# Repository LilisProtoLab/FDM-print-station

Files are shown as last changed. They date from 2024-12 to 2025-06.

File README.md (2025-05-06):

# FDM print station
For a number of FDM 3D printing materials it is of importance to store and use them under low relative humidity conditions. 
For this purpose a station was designed, containing an adapter drawer with two storage compartments, and three 3D printer compartments. For each compartment relative humidity (and temperature) can be monitored and controlled by flushing with dried compressed air. 

DSCF2053

## Main features
This FDM print station contains:
+ A humidity control system
	+ Building-supplied compressed air is fed through a membrane dryer (DM08G-19KA-N) to reduce the moisture level
   	+ Each compartment contains a sensor unit which monitors temperature, humidity and door open status
   		+ Door sensors make sure flushing is only active while the compartments are closed
   	+ Five electronic valves direct the flow of pressured air to each compartment
   	+ Dried air is distributed to five compartments: two drawer compartments, and three printer compartments
   	+ Home Assistant integration controls the humidity setpoints for the drawer compartments (typically 12%) and the printer enclosures (typically 20%)
+ One filament storage drawer with two compartments
	+ A pre-existing drawer is supplemented with a transparant PMMA enclosure for convenient selection of materials with the lids closed	
	+ A screen mounted to the drawer displays the current humidity, temperature and door sensors + flushing status of all compartments
+ Three printer enclosures
	+ vertical sliding doors for minimal obstruction from 5mm PMMA sheets, with 3D printed handles and latches.
	+  The exhaust ventilation is connected to the building exhaust system and controlled via manual, 3D printed gate valves.
	+ The enclosure is made from aluminium extrusions with 3mm PMMA sheet walls

```
.
|--- Build 
|--- Docs
|--- Results
|--- Software
| LICENSE
| README.md

```

The purpose of each subfolder is explained below:
+ Build: Contains all the (binary) design files that are needed for the hardware. Use subfolder for more complex assemblies.
+ Docs: Contains the documentation of the project: background information, sources, warnings, and build instructions. 
+ Results: For measurement or functional devices, it is good to report some results as a benchmark for others who try to replicate the project.
+ Software: For hardware projects that have an operating software or firmware, it is a good versioning practice to separate the software code from build instructions.

## Build instructions
_Guide the reader with the order of browsing your project repository for an optimum building experience_
 
When you want to start a new repository, it is better that you copy this repository to your project repository and start by changing all the description.
All instructions and (sub)headers are suggestions. You can change the style, order, or composition as you see necessary. 

It would be kind if you put a shortcut to your Bill of Materials file.
This template can be copied free of charge. 

## Outcomes

## Team
+ Project initiator: Pieter Kooijman @pkooijman
+ Contributors:
	+ Josh Hauser @catoprovector
 	+ Nico van Hijningen

## Get involved
_Especially for open source projects, it is benefitial to motivate the potential users of the project to contribute back or share their feedback. Make it easy for them._

Comments and suggestions on this folder structure are always welcome. Please create an issue to share your feedback or question, or if you prefer send a pull request. 

Better structured projects can explain a number of options for contributors such as: 
+ (where to start)
+ (issue template)
+ (direct contact)
+ (pull requests)

## License
_After the README, A LICENSE is the most important file in the project documentation. Without a license, there is too much uncertainty to try building anything on top of the original project._

This project is released under CC0 1.0 Universal. 
You can modify an reuse as you like.
The project team appreciates your suggestions or examples for enhancing the repository, but your consistent documentation of your project is the best gift to the world. Hopefully, this template could make that a bit easier for you. 

### (How to cite:)
_Additionally, you can specify how other can cite your project._

## (Funding)
_Be kind to your funders and mention their support visibly and consistently. They also need to show their resources are wisely spent._

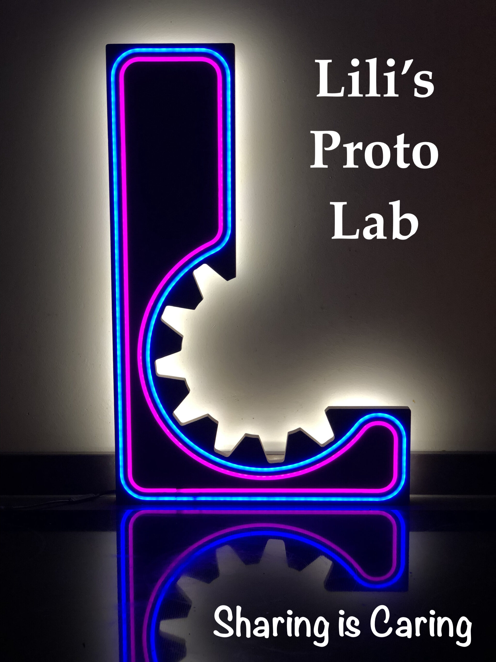
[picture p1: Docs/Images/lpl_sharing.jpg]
LPL sharing image


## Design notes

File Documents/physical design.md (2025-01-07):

# Build instructions
Contains the documentation of the project: e.g. background information, sources, warnings, and build instructions.

DSCF2064
DSCF2054
DSCF2054
DSCF2058
DSCF2058

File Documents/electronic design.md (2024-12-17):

# Electronic design

1. Functional description
The compartments (containing the rH and cover sensors) are connected with the central unit using telephone cables (RJ12 connectors).
The I2C-bus protocol is used to communicate with the rH sensors. 
A power supply (12V/2.5A) is connected to the central unit.
A 5-valve unit is connected to the central unit.

Parts:
MCU: Wemos D1 mini. The wifi enables connection with Home Assistant, it is compact, cheap, and can be programmed with the Arduino IDE. 
Humidity sensors: AM2320
Cover sensors: on/off switches
Valves: 12V solenoid type, used to provide the compartments with low rH air . 
Display: Oled 264x64, 3.1”, I2C. The MCU has a limited number of inputs/outputs, by choosing I2C, the display can be located in any of the compartments.

2. Circuit

Central unit:


The D1 mini is the central processing unit. Each valve can be activated through a mosfet (Vgs(th)<3V). The required power (needed to open a valve, and to keep it open) is controlled by changing the dutycycle of the IO-pin (v1..v5).

The 5V input is generated by a step-down regulator, and derived from the external 12V adapter.

The PCA9548 is an octal bidirectional translating switch controlled via the I2C-bus. Since the humidity sensor has a fixed I2C address, the switch enables access to one compartment at the time.

The cover sensors (s1..s5) are connected to MCP23008, an 8-bit bidirectional I/O-port, which is accessed through the I2C-bus.

Due to the longer leads, the I2C-bus frequency is limited to 100 kHz.
 

Compartment module: 


The AM2320 is directly connected with the modular 6P6C jack (RJ12).
Also, an extra connector is foreseen to enable access to a I2C-display.
The cover sensor is connected to pin 6.

The 3V3 OLED-display can also be connected to the I2C-bus. Since Vcc = 5V,  a small I2C bi-directional 5V-3.3V level converter is required. 

[def]: 2024-12-17-15-07-21.png

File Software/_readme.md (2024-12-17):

# Software instructions

3.1. Functional description
At startup, the module tries to connect with WiFi.
If it does not succeed, it opens an access point with SSID "LPL Filament Store", where you need to fill in (first time only):
	-WiFi SSID and password
	-MQTT server IP address
	-MQTT user and password
After saving the credentials the rest of the setup will continue with initialize the hardware and display a welcome message.

Then in a continuous loop:
-	there is a check for incoming mqtt-messages (setpoint update). If so, the new setpoint values are saved. Also,
-	each second a compartment is measured and checked whether a valve must be opened or closed, and the display is updated
-	calls MQTTAutodiscover::loop()
-	every 5 seconds a state message (temperature/humidity) is sent to mqtt broker

3.2. Software modules
Software: FStorageV2_xx
Arduino IDE 2.3.3

The software is split in a few separate modules (.h, .cpp), each with their own task.
FStorageV2.xx.ino:	Main file
device_config:	Hardware info: pin assignments, global definitions		
MQTTManager:	Responsible for WiFi connection, input of MQTT credentials. Is called from MQTTAutoDiscover.
MQTTAutodiscover: 
			This module takes care of:
	Initial connection with WiFi. (uses MQTTManager)
	Connection with HomeAssistant
	Sending discovery data 
	Update sensor states, receive setpoint update.
Cabinet:	Keeps track of sensor data, controls when the valves are opened or closed, depending on humidity level and cover states.

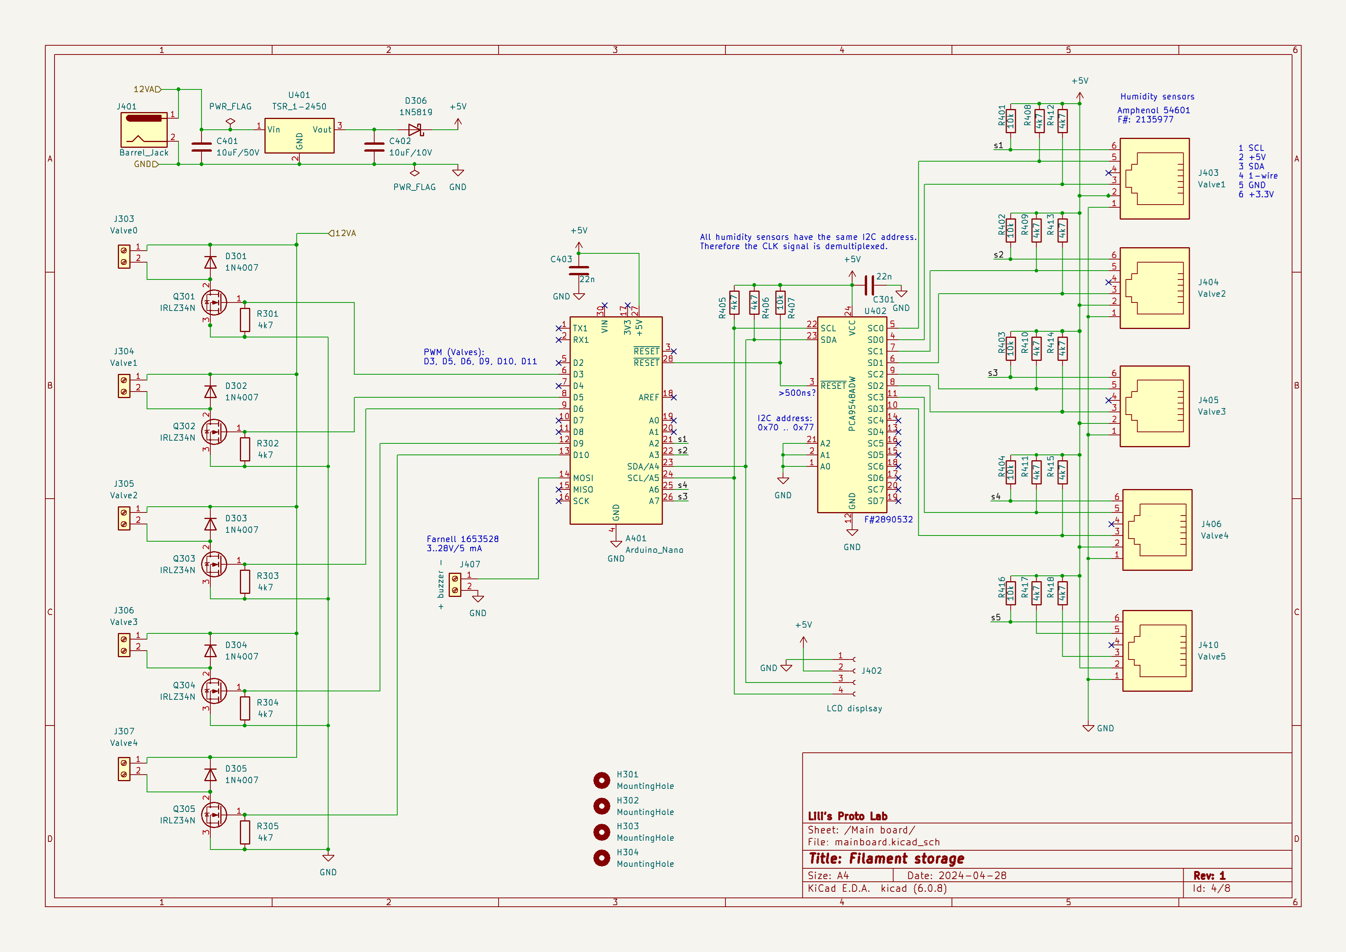
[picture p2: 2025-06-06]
Documents/V1.png

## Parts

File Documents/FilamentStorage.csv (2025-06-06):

Source: | C:\Users\nvhij\Documents\UU\Filament magazijn\Electronics\FilamentSttorage_V2_0\FilamentStorage.kicad_sch
Date: | 13/05/2024 14:26:52
Tool: | Eeschema (6.0.8)
Generator: | C:\Program Files\KiCad\6.0\bin\scripting\plugins/bom_csv_grouped_by_value.py
Component Count: | 82
Individual Components:
Item | Qty | Reference(s) | Value | LibPart | Footprint | Datasheet
 |  | C301 | 22n | Device:C | Capacitor_THT:C_Disc_D3.4mm_W2.1mm_P2.50mm | ~
 |  | C401 | 10uF/50V | Device:C | Capacitor_THT:CP_Radial_D6.3mm_P2.50mm | ~
 |  | C402 | 10uF/10V | Device:C | Capacitor_THT:CP_Radial_D6.3mm_P2.50mm | ~
 |  | C403 | 22n | Device:C | Capacitor_THT:C_Disc_D3.4mm_W2.1mm_P2.50mm | ~
 |  | C404 | 22n | Device:C | Capacitor_THT:C_Disc_D3.4mm_W2.1mm_P2.50mm | ~
 |  | D301 | 1N4007 | Diode:1N4007 | Diode_THT:D_DO-41_SOD81_P7.62mm_Horizontal | http://www.vishay.com/docs/88503/1n4001.pdf
 |  | D302 | 1N4007 | Diode:1N4007 | Diode_THT:D_DO-41_SOD81_P7.62mm_Horizontal | http://www.vishay.com/docs/88503/1n4001.pdf
 |  | D303 | 1N4007 | Diode:1N4007 | Diode_THT:D_DO-41_SOD81_P7.62mm_Horizontal | http://www.vishay.com/docs/88503/1n4001.pdf
 |  | D304 | 1N4007 | Diode:1N4007 | Diode_THT:D_DO-41_SOD81_P7.62mm_Horizontal | http://www.vishay.com/docs/88503/1n4001.pdf
 |  | D305 | 1N4007 | Diode:1N4007 | Diode_THT:D_DO-41_SOD81_P7.62mm_Horizontal | http://www.vishay.com/docs/88503/1n4001.pdf
 |  | D306 | 1N5819 | Diode:1N5819 | Diode_THT:D_DO-41_SOD81_P10.16mm_Horizontal | http://www.vishay.com/docs/88525/1n5817.pdf
 |  | H301 | MountingHole | Mechanical:MountingHole | MountingHole:MountingHole_3.2mm_M3 | ~
 |  | H302 | MountingHole | Mechanical:MountingHole | MountingHole:MountingHole_3.2mm_M3 | ~
 |  | H303 | MountingHole | Mechanical:MountingHole | MountingHole:MountingHole_3.2mm_M3 | ~
 |  | H304 | MountingHole | Mechanical:MountingHole | MountingHole:MountingHole_3.2mm_M3 | ~
 |  | J201 | 6P6C | Connector:6P6C | Connector_RJ:RJ12_Amphenol_54601 | ~
 |  | J202 | I2C | Connector_Generic:Conn_01x04 | Connector_JST:JST_PH_B4B-PH-K_1x04_P2.00mm_Vertical | ~
 |  | J203 | Screw_Terminal_01x02 | Connector:Screw_Terminal_01x02 | TerminalBlock_RND:TerminalBlock_RND_205-00287_1x02_P5.08mm_Horizontal | ~
 |  | J204 | I2C | Connector_Generic:Conn_01x04 | Connector_JST:JST_PH_B4B-PH-K_1x04_P2.00mm_Vertical | ~
 |  | J205 | 6P6C | Connector:6P6C | Connector_RJ:RJ12_Amphenol_54601 | ~
 |  | J301 | Screw_Terminal_01x02 | Connector:Screw_Terminal_01x02 | TerminalBlock_RND:TerminalBlock_RND_205-00287_1x02_P5.08mm_Horizontal | ~
 |  | J303 | Valve1 | Connector:Screw_Terminal_01x02 | TerminalBlock_RND:TerminalBlock_RND_205-00287_1x02_P5.08mm_Horizontal | ~
 |  | J304 | Valve2 | Connector:Screw_Terminal_01x02 | TerminalBlock_RND:TerminalBlock_RND_205-00287_1x02_P5.08mm_Horizontal | ~
 |  | J305 | Valve3 | Connector:Screw_Terminal_01x02 | TerminalBlock_RND:TerminalBlock_RND_205-00287_1x02_P5.08mm_Horizontal | ~
 |  | J306 | Valve4 | Connector:Screw_Terminal_01x02 | TerminalBlock_RND:TerminalBlock_RND_205-00287_1x02_P5.08mm_Horizontal | ~
 |  | J307 | Valve5 | Connector:Screw_Terminal_01x02 | TerminalBlock_RND:TerminalBlock_RND_205-00287_1x02_P5.08mm_Horizontal | ~
 |  | J401 | Barrel_Jack_Switch | Connector:Barrel_Jack_Switch | Connector_BarrelJack:BarrelJack_Wuerth_6941xx301002 | ~
 |  | J402 | LCD displsay | Connector:Conn_01x04_Female | NVH_Library:PinHeader_1x04_P2.54mm_Horizontal_1left | ~
 |  | J403 | Valve1 | Connector:6P6C | Connector_RJ:RJ12_Amphenol_54601 | ~
 |  | J404 | Valve2 | Connector:6P6C | Connector_RJ:RJ12_Amphenol_54601 | ~
 |  | J405 | Valve3 | Connector:6P6C | Connector_RJ:RJ12_Amphenol_54601 | ~
 |  | J406 | Valve4 | Connector:6P6C | Connector_RJ:RJ12_Amphenol_54601 | ~
 |  | J407 | + buzzer - | Connector:Screw_Terminal_01x02 | TerminalBlock_RND:TerminalBlock_RND_205-00287_1x02_P5.08mm_Horizontal | ~
 |  | J408 | 6P6C | Connector:6P6C | Connector_RJ:RJ12_Amphenol_54601 | ~
 |  | J409 | I2C | Connector_Generic:Conn_01x04 | Connector_JST:JST_PH_B4B-PH-K_1x04_P2.00mm_Vertical | ~
 |  | J410 | Valve5 | Connector:6P6C | Connector_RJ:RJ12_Amphenol_54601 | ~
 |  | J501 | Screw_Terminal_01x02 | Connector:Screw_Terminal_01x02 | TerminalBlock_RND:TerminalBlock_RND_205-00287_1x02_P5.08mm_Horizontal | ~
 |  | J601 | 6P6C | Connector:6P6C | Connector_RJ:RJ12_Amphenol_54601 | ~
 |  | J602 | I2C | Connector_Generic:Conn_01x04 | Connector_JST:JST_PH_B4B-PH-K_1x04_P2.00mm_Vertical | ~
 |  | J701 | Screw_Terminal_01x02 | Connector:Screw_Terminal_01x02 | TerminalBlock_RND:TerminalBlock_RND_205-00287_1x02_P5.08mm_Horizontal | ~
 |  | J702 | 6P6C | Connector:6P6C | Connector_RJ:RJ12_Amphenol_54601 | ~
 |  | J703 | I2C | Connector_Generic:Conn_01x04 | Connector_JST:JST_PH_B4B-PH-K_1x04_P2.00mm_Vertical | ~
 |  | J801 | Screw_Terminal_01x02 | Connector:Screw_Terminal_01x02 | TerminalBlock_RND:TerminalBlock_RND_205-00287_1x02_P5.08mm_Horizontal | ~
 |  | Q301 | IRLZ34N | Transistor_FET:IRLZ34N | Package_TO_SOT_THT:TO-220-3_Vertical | http://www.infineon.com/dgdl/irlz34npbf.pdf?fileId=5546d462533600a40153567206892720
 |  | Q302 | IRLZ34N | Transistor_FET:IRLZ34N | Package_TO_SOT_THT:TO-220-3_Vertical | http://www.infineon.com/dgdl/irlz34npbf.pdf?fileId=5546d462533600a40153567206892720
 |  | Q303 | IRLZ34N | Transistor_FET:IRLZ34N | Package_TO_SOT_THT:TO-220-3_Vertical | http://www.infineon.com/dgdl/irlz34npbf.pdf?fileId=5546d462533600a40153567206892720
 |  | Q304 | IRLZ34N | Transistor_FET:IRLZ34N | Package_TO_SOT_THT:TO-220-3_Vertical | http://www.infineon.com/dgdl/irlz34npbf.pdf?fileId=5546d462533600a40153567206892720
 |  | Q305 | IRLZ34N | Transistor_FET:IRLZ34N | Package_TO_SOT_THT:TO-220-3_Vertical | http://www.infineon.com/dgdl/irlz34npbf.pdf?fileId=5546d462533600a40153567206892720
 |  | R301 | 4k7 | Device:R | Resistor_THT:R_Axial_DIN0207_L6.3mm_D2.5mm_P7.62mm_Horizontal | ~
 |  | R302 | 4k7 | Device:R | Resistor_THT:R_Axial_DIN0207_L6.3mm_D2.5mm_P7.62mm_Horizontal | ~
 |  | R303 | 4k7 | Device:R | Resistor_THT:R_Axial_DIN0207_L6.3mm_D2.5mm_P7.62mm_Horizontal | ~
 |  | R304 | 4k7 | Device:R | Resistor_THT:R_Axial_DIN0207_L6.3mm_D2.5mm_P7.62mm_Horizontal | ~
 |  | R305 | 4k7 | Device:R | Resistor_THT:R_Axial_DIN0207_L6.3mm_D2.5mm_P7.62mm_Horizontal | ~
 |  | R401 | 10k | Device:R | Resistor_THT:R_Axial_DIN0207_L6.3mm_D2.5mm_P7.62mm_Horizontal | ~
 |  | R402 | 10k | Device:R | Resistor_THT:R_Axial_DIN0207_L6.3mm_D2.5mm_P7.62mm_Horizontal | ~
 |  | R403 | 10k | Device:R | Resistor_THT:R_Axial_DIN0207_L6.3mm_D2.5mm_P7.62mm_Horizontal | ~
 |  | R404 | 10k | Device:R | Resistor_THT:R_Axial_DIN0207_L6.3mm_D2.5mm_P7.62mm_Horizontal | ~
 |  | R405 | 4k7 | Device:R | Resistor_THT:R_Axial_DIN0207_L6.3mm_D2.5mm_P7.62mm_Horizontal | ~
 |  | R406 | 4k7 | Device:R | Resistor_THT:R_Axial_DIN0207_L6.3mm_D2.5mm_P7.62mm_Horizontal | ~
 |  | R407 | 10k | Device:R | Resistor_THT:R_Axial_DIN0207_L6.3mm_D2.5mm_P7.62mm_Horizontal | ~
 |  | R408 | 4k7 | Device:R | Resistor_THT:R_Axial_DIN0207_L6.3mm_D2.5mm_P7.62mm_Horizontal | ~
 |  | R409 | 4k7 | Device:R | Resistor_THT:R_Axial_DIN0207_L6.3mm_D2.5mm_P7.62mm_Horizontal | ~
 |  | R410 | 4k7 | Device:R | Resistor_THT:R_Axial_DIN0207_L6.3mm_D2.5mm_P7.62mm_Horizontal | ~
 |  | R411 | 4k7 | Device:R | Resistor_THT:R_Axial_DIN0207_L6.3mm_D2.5mm_P7.62mm_Horizontal | ~
 |  | R412 | 4k7 | Device:R | Resistor_THT:R_Axial_DIN0207_L6.3mm_D2.5mm_P7.62mm_Horizontal | ~
 |  | R413 | 4k7 | Device:R | Resistor_THT:R_Axial_DIN0207_L6.3mm_D2.5mm_P7.62mm_Horizontal | ~
 |  | R414 | 4k7 | Device:R | Resistor_THT:R_Axial_DIN0207_L6.3mm_D2.5mm_P7.62mm_Horizontal | ~
 |  | R415 | 4k7 | Device:R | Resistor_THT:R_Axial_DIN0207_L6.3mm_D2.5mm_P7.62mm_Horizontal | ~
 |  | R416 | 10k | Device:R | Resistor_THT:R_Axial_DIN0207_L6.3mm_D2.5mm_P7.62mm_Horizontal | ~
 |  | R417 | 4k7 | Device:R | Resistor_THT:R_Axial_DIN0207_L6.3mm_D2.5mm_P7.62mm_Horizontal | ~
 |  | R418 | 4k7 | Device:R | Resistor_THT:R_Axial_DIN0207_L6.3mm_D2.5mm_P7.62mm_Horizontal | ~
 |  | R419 | 4k7 | Device:R | Resistor_THT:R_Axial_DIN0207_L6.3mm_D2.5mm_P7.62mm_Horizontal | ~
 |  | R420 | 4k7 | Device:R | Resistor_THT:R_Axial_DIN0207_L6.3mm_D2.5mm_P7.62mm_Horizontal | ~
 |  | U201 | AM2320 | NVH_Library:AM2320 | NVH_Library:AM2320_horizontal
 |  | U301 | AM2320 | NVH_Library:AM2320 | NVH_Library:AM2320_horizontal
 |  | U401 | TSR_1-2450 | Regulator_Switching:TSR_1-2450 | Converter_DCDC:Converter_DCDC_TRACO_TSR-1_THT | http://www.tracopower.com/products/tsr1.pdf
 |  | U402 | PCA9548ADW | Interface_Expansion:PCA9548ADW | Package_SO:SOIC-24W_7.5x15.4mm_P1.27mm | http://www.ti.com/lit/ds/symlink/pca9548a.pdf
 |  | U403 | WeMos_D1_mini V3 | MCU_Module:WeMos_D1_mini | Module:WEMOS_D1_mini_light | https://wiki.wemos.cc/products:d1:d1_mini#documentation
 |  | U404 | MCP23008-xSO | Interface_Expansion:MCP23008-xSO | Package_SO:SOIC-18W_7.5x11.6mm_P1.27mm | http://ww1.microchip.com/downloads/en/DeviceDoc/MCP23008-MCP23S08-Data-Sheet-20001919F.pdf
 |  | U501 | AM2320 | NVH_Library:AM2320 | NVH_Library:AM2320_horizontal
 |  | U701 | AM2320 | NVH_Library:AM2320 | NVH_Library:AM2320_horizontal
 |  | U801 | AM2320 | NVH_Library:AM2320 | NVH_Library:AM2320_horizontal
Collated Components:
Item | Qty | Reference(s) | Value | LibPart | Footprint | Datasheet
1 | 3 | C301, C403, C404 | 22n | Device:C | Capacitor_THT:C_Disc_D3.4mm_W2.1mm_P2.50mm | ~
2 | 1 | C401 | 10uF/50V | Device:C | Capacitor_THT:CP_Radial_D6.3mm_P2.50mm | ~
3 | 1 | C402 | 10uF/10V | Device:C | Capacitor_THT:CP_Radial_D6.3mm_P2.50mm | ~
4 | 5 | D301, D302, D303, D304, D305 | 1N4007 | Diode:1N4007 | Diode_THT:D_DO-41_SOD81_P7.62mm_Horizontal | http://www.vishay.com/docs/88503/1n4001.pdf
5 | 1 | D306 | 1N5819 | Diode:1N5819 | Diode_THT:D_DO-41_SOD81_P10.16mm_Horizontal | http://www.vishay.com/docs/88525/1n5817.pdf
6 | 4 | H301, H302, H303, H304 | MountingHole | Mechanical:MountingHole | MountingHole:MountingHole_3.2mm_M3 | ~
7 | 5 | J201, J205, J408, J601, J702 | 6P6C | Connector:6P6C | Connector_RJ:RJ12_Amphenol_54601 | ~
8 | 5 | J202, J204, J409, J602, J703 | I2C | Connector_Generic:Conn_01x04 | Connector_JST:JST_PH_B4B-PH-K_1x04_P2.00mm_Vertical | ~
9 | 5 | J203, J301, J501, J701, J801 | Screw_Terminal_01x02 | Connector:Screw_Terminal_01x02 | TerminalBlock_RND:TerminalBlock_RND_205-00287_1x02_P5.08mm_Horizontal | ~
10 | 1 | J303 | Valve1 | Connector:Screw_Terminal_01x02 | TerminalBlock_RND:TerminalBlock_RND_205-00287_1x02_P5.08mm_Horizontal | ~
11 | 1 | J304 | Valve2 | Connector:Screw_Terminal_01x02 | TerminalBlock_RND:TerminalBlock_RND_205-00287_1x02_P5.08mm_Horizontal | ~
12 | 1 | J305 | Valve3 | Connector:Screw_Terminal_01x02 | TerminalBlock_RND:TerminalBlock_RND_205-00287_1x02_P5.08mm_Horizontal | ~
13 | 1 | J306 | Valve4 | Connector:Screw_Terminal_01x02 | TerminalBlock_RND:TerminalBlock_RND_205-00287_1x02_P5.08mm_Horizontal | ~
14 | 1 | J307 | Valve5 | Connector:Screw_Terminal_01x02 | TerminalBlock_RND:TerminalBlock_RND_205-00287_1x02_P5.08mm_Horizontal | ~
15 | 1 | J401 | Barrel_Jack_Switch | Connector:Barrel_Jack_Switch | Connector_BarrelJack:BarrelJack_Wuerth_6941xx301002 | ~
16 | 1 | J402 | LCD displsay | Connector:Conn_01x04_Female | NVH_Library:PinHeader_1x04_P2.54mm_Horizontal_1left | ~
17 | 1 | J403 | Valve1 | Connector:6P6C | Connector_RJ:RJ12_Amphenol_54601 | ~
18 | 1 | J404 | Valve2 | Connector:6P6C | Connector_RJ:RJ12_Amphenol_54601 | ~
19 | 1 | J405 | Valve3 | Connector:6P6C | Connector_RJ:RJ12_Amphenol_54601 | ~
20 | 1 | J406 | Valve4 | Connector:6P6C | Connector_RJ:RJ12_Amphenol_54601 | ~
21 | 1 | J407 | + buzzer - | Connector:Screw_Terminal_01x02 | TerminalBlock_RND:TerminalBlock_RND_205-00287_1x02_P5.08mm_Horizontal | ~
22 | 1 | J410 | Valve5 | Connector:6P6C | Connector_RJ:RJ12_Amphenol_54601 | ~
23 | 5 | Q301, Q302, Q303, Q304, Q305 | IRLZ34N | Transistor_FET:IRLZ34N | Package_TO_SOT_THT:TO-220-3_Vertical | http://www.infineon.com/dgdl/irlz34npbf.pdf?fileId=5546d462533600a40153567206892720
24 | 19 | R301, R302, R303, R304, R305, R405, R406, R408, R409, R410, R411, R412, R413, R414, R415, R417, R418, R419, R420 | 4k7 | Device:R | Resistor_THT:R_Axial_DIN0207_L6.3mm_D2.5mm_P7.62mm_Horizontal | ~
25 | 6 | R401, R402, R403, R404, R407, R416 | 10k | Device:R | Resistor_THT:R_Axial_DIN0207_L6.3mm_D2.5mm_P7.62mm_Horizontal | ~
26 | 5 | U201, U301, U501, U701, U801 | AM2320 | NVH_Library:AM2320 | NVH_Library:AM2320_horizontal
27 | 1 | U401 | TSR_1-2450 | Regulator_Switching:TSR_1-2450 | Converter_DCDC:Converter_DCDC_TRACO_TSR-1_THT | http://www.tracopower.com/products/tsr1.pdf
28 | 1 | U402 | PCA9548ADW | Interface_Expansion:PCA9548ADW | Package_SO:SOIC-24W_7.5x15.4mm_P1.27mm | http://www.ti.com/lit/ds/symlink/pca9548a.pdf
29 | 1 | U403 | WeMos_D1_mini V3 | MCU_Module:WeMos_D1_mini | Module:WEMOS_D1_mini_light | https://wiki.wemos.cc/products:d1:d1_mini#documentation
30 | 1 | U404 | MCP23008-xSO | Interface_Expansion:MCP23008-xSO | Package_SO:SOIC-18W_7.5x11.6mm_P1.27mm | http://ww1.microchip.com/downloads/en/DeviceDoc/MCP23008-MCP23S08-Data-Sheet-20001919F.pdf

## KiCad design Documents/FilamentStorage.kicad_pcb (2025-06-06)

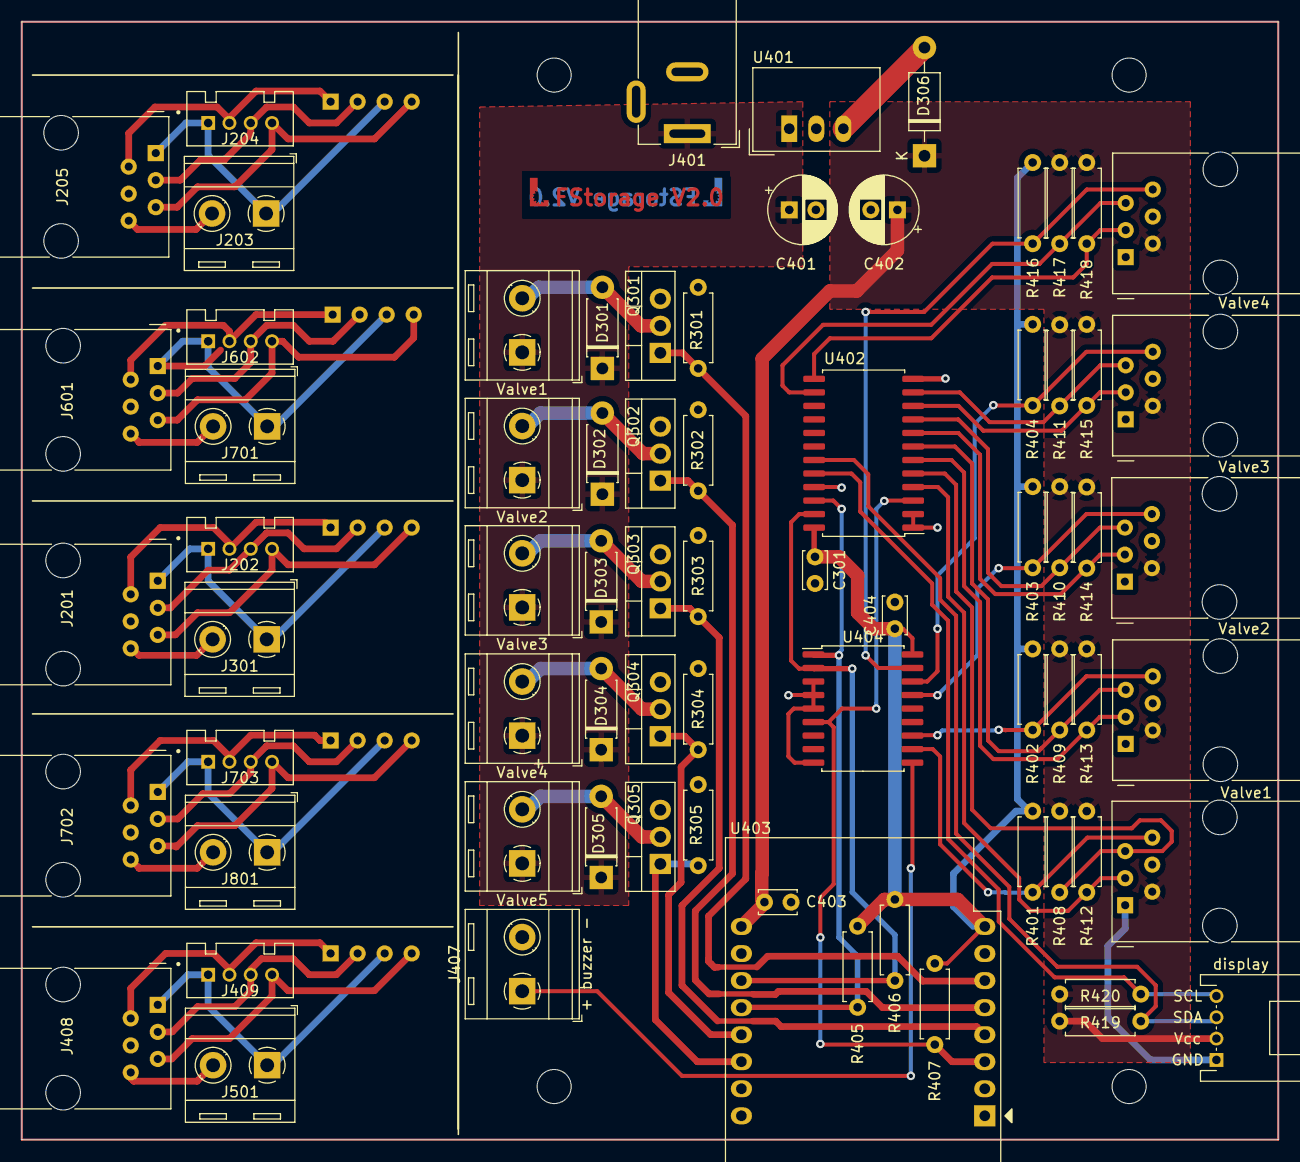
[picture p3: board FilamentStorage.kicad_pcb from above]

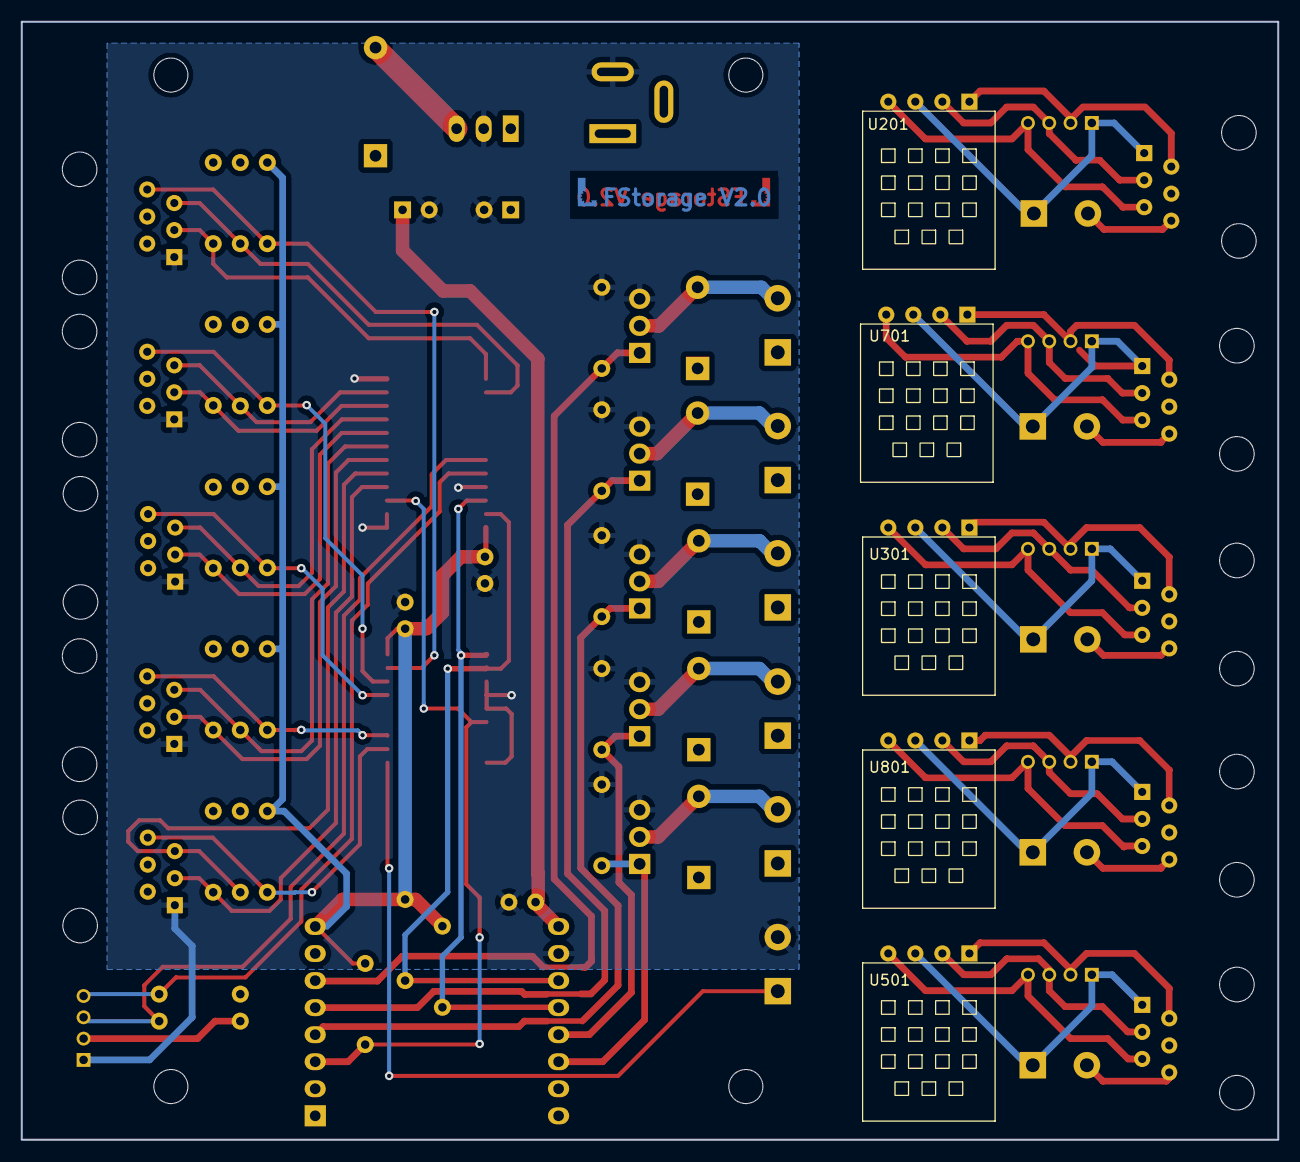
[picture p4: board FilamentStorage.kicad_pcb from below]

Board: 2 copper layers, 118.0 x 105.0 mm, 82 parts (5 on the bottom side), 61 nets.

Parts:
C301, C403, C404: 22n; C_Disc_D3.4mm_W2.1mm_P2.50mm
C401: 10uF/50V; CP_Radial_D6.3mm_P2.50mm
C402: 10uF/10V; CP_Radial_D6.3mm_P2.50mm
D301, D302, D303, D304, D305: 1N4007; D_DO-41_SOD81_P7.62mm_Horizontal
D306: 1N5817; D_DO-41_SOD81_P10.16mm_Horizontal
H301, H302, H303, H304: MountingHole; MountingHole_3.2mm_M3
J201, J205, J408, J601, J702: 6P6C; RJ12_Amphenol_54601
J202, J204, J409, J602, J703: I2C; grove_4p_vert
J203, J301, J501, J701, J801: Screw_Terminal_01x02; TerminalBlock_RND_205-00287_1x02_P5.08mm_Horizontal
J303: Valve1; TerminalBlock_RND_205-00287_1x02_P5.08mm_Horizontal
J304: Valve2; TerminalBlock_RND_205-00287_1x02_P5.08mm_Horizontal
J305: Valve3; TerminalBlock_RND_205-00287_1x02_P5.08mm_Horizontal
J306: Valve4; TerminalBlock_RND_205-00287_1x02_P5.08mm_Horizontal
J307: Valve5; TerminalBlock_RND_205-00287_1x02_P5.08mm_Horizontal
J401: Barrel_Jack_Switch; BarrelJack_Wuerth_6941xx301002
J402: display; grove_4p_hor
J403: Valve1; RJ12_Amphenol_54601
J404: Valve2; RJ12_Amphenol_54601
J405: Valve3; RJ12_Amphenol_54601
J406: Valve4; RJ12_Amphenol_54601
J407: + buzzer -; TerminalBlock_RND_205-00287_1x02_P5.08mm_Horizontal
J410: Valve5; RJ12_Amphenol_54601
Q301, Q302, Q303, Q304, Q305: IRLZ34N; TO-220-3_Vertical
R301, R302, R303, R304, R305, R405, R406, R408, R409, R410, R411, R412, R413, R414, R415, R417, R418, R419, R420: 4k7; R_Axial_DIN0207_L6.3mm_D2.5mm_P7.62mm_Horizontal
R401, R402, R403, R404, R407, R416: 10k; R_Axial_DIN0207_L6.3mm_D2.5mm_P7.62mm_Horizontal
U201, U301, U501, U701, U801: AM2320; AM2320_horizontal
U401: TSR_1-2450; Converter_DCDC_TRACO_TSR-1_THT
U402: PCA9548ADW; SOIC-24W_7.5x15.4mm_P1.27mm
U403: WeMos_D1_mini V3; WEMOS_D1_mini_light
U404: MCP23008-xSO; SOIC-18W_7.5x11.6mm_P1.27mm

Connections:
+3V3: C301.1, C404.1, R401.2, R402.2, R403.2, R404.2, R405.2, R406.2, R407.2, R416.2, U402.24 (VCC), U403.8 (3V3), U404.18 (VDD)
+5V: C402.1, C403.1, D306.1 (K), J402.2, J403.2, J404.2, J405.2, J406.2, J410.2, R408.1, R409.1, R410.1, R411.1, R412.1, R413.1, R414.1, R415.1, R417.1, R418.1, R419.2, R420.2, U403.9 (5V)
/12VA: C401.1, D301.1 (K), D302.1 (K), D303.1 (K), D304.1 (K), D305.1 (K), J303.1, J304.1, J305.1, J306.1, J307.1, J401.1, U401.1 (Vin)
/Cabinet1/shield: J408.1, J409.1, J501.1, U501.3 (gnd)
/Cabinet2/shield: J601.1, J602.1, J701.1, U701.3 (gnd)
/Cabinet3/shield: J702.1, J703.1, J801.1, U801.3 (gnd)
/Cabinet4/shield: J203.1, J204.1, J205.1, U201.3 (gnd)
/Cabinet/shield: J201.1, J202.1, J301.1, U301.3 (gnd)
/Main board/b1: J407.1, U404.10 (GP0)
/Main board/s1: J403.6, R401.1, U404.11 (GP1)
/Main board/s2: J404.6, R402.1, U404.12 (GP2)
/Main board/s3: J405.6, R403.1, U404.15 (GP5)
/Main board/s4: J406.6, R404.1, U404.16 (GP6)
/Main board/s5: J410.6, R416.1, U404.17 (GP7)
/Main board/v1: Q301.1 (G), R301.1, U403.6 (MOSI/D7)
/Main board/v2: Q302.1 (G), R302.1, U403.5 (MISO/D6)
/Main board/v3: Q303.1 (G), R303.1, U403.4 (SCK/D5)
/Main board/v4: Q304.1 (G), R304.1, U403.13 (SDA/D2)
/Main board/v5: Q305.1 (G), R305.1, U403.14 (SCL/D1)
GND: C301.2, C401.2, C402.2, C403.2, C404.2, J401.2, J402.1, J403.1, J404.1, J405.1, J406.1, J407.2, J410.1, Q301.3 (S), Q302.3 (S), Q303.3 (S), Q304.3 (S), Q305.3 (S), R301.2, R302.2, R303.2, R304.2, R305.2, U401.2 (GND), U402.1 (A0), U402.2 (A1), U402.12 (GND), U402.21 (A2), U403.10 (GND), U404.3 (A2), U404.4 (A1), U404.5 (A0), U404.9 (VSS)
unnamed: D301.2 (A), J303.2, Q301.2 (D)
unnamed: D302.2 (A), J304.2, Q302.2 (D)
unnamed: D303.2 (A), J305.2, Q303.2 (D)
unnamed: D304.2 (A), J306.2, Q304.2 (D)
unnamed: D305.2 (A), J307.2, Q305.2 (D)
unnamed: D306.2 (A), U401.3 (Vout)
unnamed: J201.2, J202.2, U301.1 (Vcc)
unnamed: J201.3, J202.3, U301.2 (SDA)
unnamed: J201.5, J202.4, U301.4 (SCL)
unnamed: J201.6, J301.2
unnamed: J203.2, J205.6
unnamed: J204.2, J205.2, U201.1 (Vcc)
unnamed: J204.3, J205.3, U201.2 (SDA)
unnamed: J204.4, J205.5, U201.4 (SCL)
unnamed: J402.3, R419.1, U402.19 (SD7)
unnamed: J402.4, R420.1, U402.20 (SC7)
unnamed: J403.3, R412.2, U402.4 (SD0)
unnamed: J403.5, R408.2, U402.5 (SC0)
unnamed: J404.3, R413.2, U402.6 (SD1)
unnamed: J404.5, R409.2, U402.7 (SC1)
unnamed: J405.3, R414.2, U402.8 (SD2)
unnamed: J405.5, R410.2, U402.9 (SC2)
unnamed: J406.3, R415.2, U402.10 (SD3)
unnamed: J406.5, R411.2, U402.11 (SC3)
unnamed: J408.2, J409.2, U501.1 (Vcc)
unnamed: J408.3, J409.3, U501.2 (SDA)
unnamed: J408.5, J409.4, U501.4 (SCL)
unnamed: J408.6, J501.2
unnamed: J410.3, R418.2, U402.13 (SD4)
unnamed: J410.5, R417.2, U402.14 (SC4)
unnamed: J601.2, J602.2, U701.1 (Vcc)
unnamed: J601.3, J602.3, U701.2 (SDA)
unnamed: J601.5, J602.4, U701.4 (SCL)
unnamed: J601.6, J701.2
unnamed: J702.2, J703.2, U801.1 (Vcc)
unnamed: J702.3, J703.3, U801.2 (SDA)
unnamed: J702.5, J703.4, U801.4 (SCL)
unnamed: J702.6, J801.2
unnamed: R405.1, U402.22 (SCL), U403.12 (D3), U404.1 (SCL)
unnamed: R406.1, U402.23 (SDA), U403.11 (D4), U404.2 (SDA)
unnamed: R407.1, U402.3 (~RESET), U403.3 (D0), U404.6 (~RESET)

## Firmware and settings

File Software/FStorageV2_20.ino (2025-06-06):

#include <Wire.h>
#include <MCP23008.h>
#include <Adafruit_AM2320.h>
#include <U8g2lib.h>
#include "device_config.h"
#include "cabinet.h"
#include "MQTTAutodiscover.h"


//#define debug_print  // remove to disable serial output
#include <NHDebug.h>

//#define SKIPWIFI

U8G2_SSD1309_128X64_NONAME2_F_HW_I2C  u8g2(U8G2_R0) ;  //??software??
Cabinets cabs;
MCP23008 MCP(mcpAddr);
Adafruit_AM2320 am2320 = Adafruit_AM2320();
uint8_t displaychannel;
MQTTDiscover mqtt;


unsigned long refreshTime;

/******** forward declarations ********/
//main functions:
void ledToggle(void);
bool isConnected(uint8_t addr);  //I2C check
bool PCA_Select(uint8_t channel); //i2c switch to cabinet
void readCabinet(uint8_t cab); //read sensors
//display
bool initDisplay(void);
void Hello(void);
void testDisplay(void);
void updateState(void);  //send temperature/humidity data
//debug:
void binString(char* str, uint8_t value );
void debugCabinet(uint8_t cab);
void debugMeasure(uint8_t cab, float& hum, float& temp, uint8_t& doors);

/****** end forward declarations ******/



void setup() {
  pinMode(LED_BUILTIN, OUTPUT);
  debug_begin(115200);
  Wire.begin(sdaPin, sclPin);
  initDisplay();

  #ifndef SKIPWIFI
    u8g2.drawStr(0,12+12*1,"autoconnect wifi");	
    u8g2.sendBuffer();					// transfer internal memory to the display
    mqtt.begin();  // connect WiFi, HomeAssistant
  #endif

//  Wire.begin(sdaPin, sclPin);
  MCP.begin();
  MCP.pinMode8(0xFE); // 0=output
//  initDisplay();
  Hello();
  am2320.begin();

  debugln();
  debugln("loading config");
  loadConfig();

  refreshTime = millis();
}

/* measure one cabinet each second, refresh delay. update state every 5 seconds */
uint8_t activecab = 0;
uint16_t loopcount = 0; // for debug cabinets
bool STATEFLAG = false;  //update has every 5 loops


void loop() { 
  ++loopcount;

  #ifndef SKIPWIFI
    if (!mqtt.loop() ) { debugln("mqtt reconnect error");}
    if (STATEFLAG) { updateState(); STATEFLAG = false; } //each 5 loops
  #endif

  if (millis()>refreshTime) { //update each second
    ledToggle();
    readCabinet(activecab);  //also update display
    //debugCabinet(activecab);  //also update display
    //testDisplay(activecab);
    activecab = (activecab<4) ? (activecab+1) : 0;
    STATEFLAG = (activecab==0);
    refreshTime = millis() + REFRESH_DELAY;  
  }

  if (deviceconfig.changed) {
    debugln("saving config");
    saveConfig();
    debug("setpoints: "); debug(deviceconfig.setpoint[spDrawer]); debug(", "); debugln(deviceconfig.setpoint[spPrinter]); 
    mqtt.updateSetpointState();
  }

}

void ledToggle(void) {
  digitalWrite(LED_BUILTIN,!digitalRead(LED_BUILTIN));
}

void readCabinet(uint8_t cab) {
float hum, temp;
uint8_t doors;
char line[20];
  PCA_Select(cab);
  doors = MCP.read8();
  temp = am2320.readTemperature();
  hum = am2320.readHumidity();
  doors = cabs.update(line, cab, hum, temp, doors);  // save data, check checkpoint
  /* update display */
  if (PCA_Select(displaychannel) ) {
    u8g2.drawStr(0,12+12*cab,line);	
    debug ("doors="); debugln(doors);
    for (uint8_t i=0; i<NROFCABS; i++) {
      if (doors & 0x01) { strcpy(line,"# "); }
      else { strcpy(line,"  "); }
      if (cabs.valveOpen(i)) {line[1]=187; }
      u8g2.drawStr(18*6,12+12*i,line);	
      doors = doors >> 1;
    }
    u8g2.sendBuffer();					// transfer internal memory to the display
  }
}

void debugCabinet(uint8_t cab) {
float hum, temp;
uint8_t doors;
char line[20];
uint8_t valve;
  //debugln();
  //debug("**** testing cab "); debug(cab); debugln(" ****");
  debugMeasure(cab, hum, temp, doors);
  PCA_Select(cab);
  valve = cabs.update(line, cab, hum, temp, doors);  // save data
  if (PCA_Select(displaychannel) ) {
    u8g2.drawStr(0,12+12*cab,line);	// write a line
    u8g2.sendBuffer();					// transfer internal memory to the display
  }
  //debugln(line);
}

void debugMeasure(uint8_t cab, float& hum, float& temp, uint8_t& doors) {
  hum = 15 + 5*sin(0.01*PI*loopcount+cab);
  temp = 20.4 + cab + cab/10;
  doors = 0; // all doors closed
}

void updateState(void) {
String payload;
  cabs.state(payload);  //get payload
 // debugln("state payload:"); debugln(payload);
  mqtt.updateState(payload);
}


/*********** display ***********/

bool initDisplay(void) {
  displaychannel = 0xFF;
  for (uint8_t i=0; i<7; i++) {
    PCA_Select(i);
    if (isConnected(oledAddr)) { 
      displaychannel = i;
      u8g2.setBusClock(100000);
      u8g2.begin();
      u8g2.setFont(u8g2_font_6x10_mf);
//      Hello();
      u8g2.clearBuffer();	// clear the internal memory
      return(true);
    }
  }
  debug("display not found. Channel="); debugln(displaychannel);
  return(false);
}

void Hello(void) {
  if (!PCA_Select(displaychannel)) { return; };
  u8g2.clearBuffer();	
  u8g2.drawStr(0,12+12*0,"Lili's proto lab");	
  u8g2.drawStr(0,12+12*1,"Filament storage");	
  u8g2.drawStr(0,12+12*2,"humidity control");	
char version[] = SW_VERSION;
char line[20];
  strcpy(line, "software version ");
  strcat(line, version);
  u8g2.drawStr(0,12+12*3,line);	
  u8g2.sendBuffer();					// transfer internal memory to the display
  delay(2000);
  u8g2.clearBuffer();	
}


void testDisplay(uint8_t cab) {
char line[22];
  u8g2.clearBuffer();	
  strcpy(line,"X***************X");
  for (uint8_t i=0; i<10; i++) {
    line[i+1] = 181+i;
  }
//  strcpy(line, "123456789012345678901");
  u8g2.drawStr(0,12+12*1,line);	
  if (cab%2) { strcpy(line,"01"); }
  else {strcpy(line,"  ");}
  u8g2.drawStr(6*19,12+12*2,line);	

  u8g2.sendBuffer();					// transfer internal memory to the display
}



/****** measurements *****/

bool isConnected(uint8_t addr) {
  Wire.beginTransmission(addr);
  return ( Wire.endTransmission() == 0);
}

bool PCA_Select(uint8_t channel) {
  if (channel>7) { return(false); }
  Wire.beginTransmission(pcaAddr);
  Wire.write(0x01 << channel);
  Wire.endTransmission();  
  delay(100);
  return(true);
}

void binString(char* str, uint8_t value ) {
uint8_t mask = 0x80;
  strcpy(str, "00000000");
  for (uint8_t i=0; i<8; i++) {
    if ((value & mask) > 0) { str[i]='1'; } 
    mask = mask >> 1;  
  }
}

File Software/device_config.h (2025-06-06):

#ifndef DEVICE_CONFIG_H
#define DEVICE_CONFIG_H

/*
* The system consists of 5 cabinets: 2 drawers (left/right) and 3 printers (no4/5/6)
* Each cabinet has a temperature-, humidity- and door-sensor
* The printers and drawers have a separate setpoint for humidity
*/

#include <arduino.h>
#include <stdint.h>

#define HW_VERSION "1.0"
#define SW_VERSION "2.20"


//cabinet names
#define NROFCABINETS 5
/*pca channels I2C switch cab0..4 ~ channel 0..4 */
#define CABNAMES {"drawerL", "drawerR", "printer4", "printer5", "printer6"}
#define CABSHORTNAMES {"DL", "DR", "P4", "P5", "XL"}
#define VALVEPINS {D1, D2, D5, D6, D7}
#define DOORMASKS {0x02, 0x04, 0x20, 0x40, 0x80}
#define REFRESH_DELAY 1000


/*** hardware connections ***/
#define sdaPin D4
#define sclPin D3
#define pcaAddr 0x70
#define mcpAddr 0x20
#define am2320Addr 0x5C
#define oledAddr 0x3C


typedef enum {spDrawer, spPrinter, spCount} setpoint_t;

#define configfilename "/devconfig"
#define setpoint_min 5
#define setpoint_max 30
#define setpoint_margin 1  
typedef struct {
  int setpoint[spCount];
  bool changed = false;
}deviceconfig_t;



bool loadConfig (void);
bool saveConfig (void);


extern deviceconfig_t deviceconfig;


#endif
